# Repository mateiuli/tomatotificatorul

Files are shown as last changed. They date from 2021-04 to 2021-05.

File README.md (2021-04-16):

# tomatotificatorul
A simple automatic balcony plants (tomatos) watering system powered by sun.

# Parts List
## The battery
The battery I chose was a 12V, 1.4Ah, Sealed, Lead Acid Battery. I bought it from [here](https://www.caranda.ro/product/acumulator-12v-1-4ah-fp1214-stationar-agm-vrla/) for ~7$.
The box is designed for this very battery. Its dimensions are the following: 97 x 43 x 52 x 58mm

## The pump
I bought a brand new washer pump compatible with BMW/Mercedes Benz and others. You can easily find it from any car parts vendor. The part code is: FEBI BILSTEIN 23113.

## The solar panel
I found a 5W solar panel with a solid construction and sturdy frame. 

## Electronics

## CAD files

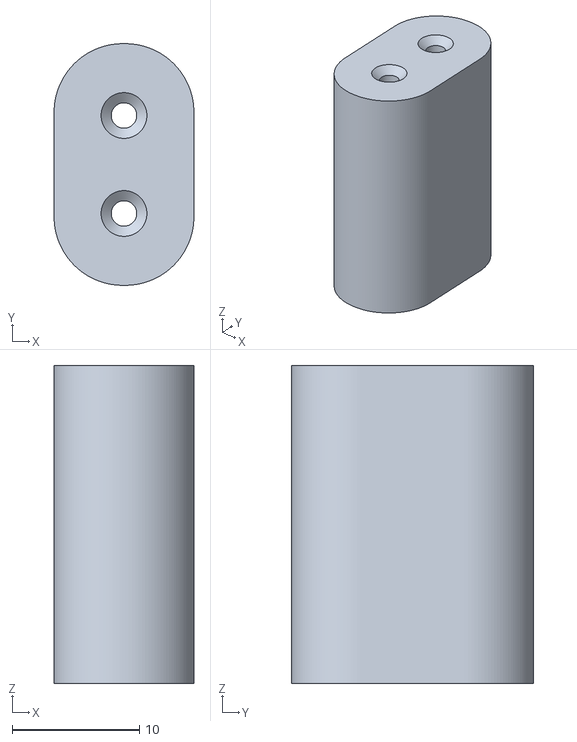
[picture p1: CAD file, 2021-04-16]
3d_objects/12v_pump_plug.stl
11.0 x 19.0 x 25.0

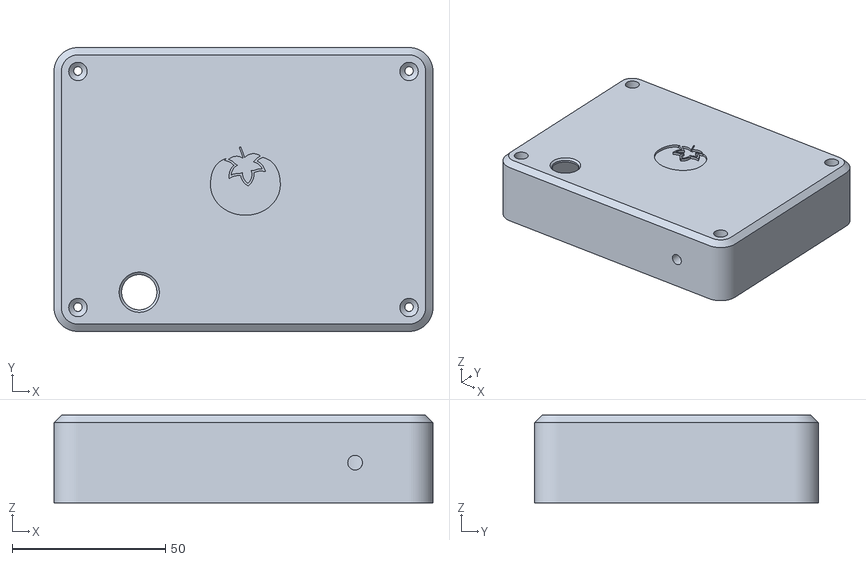
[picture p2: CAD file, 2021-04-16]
3d_objects/box_lid.stl
123.6 x 92.6 x 28.6

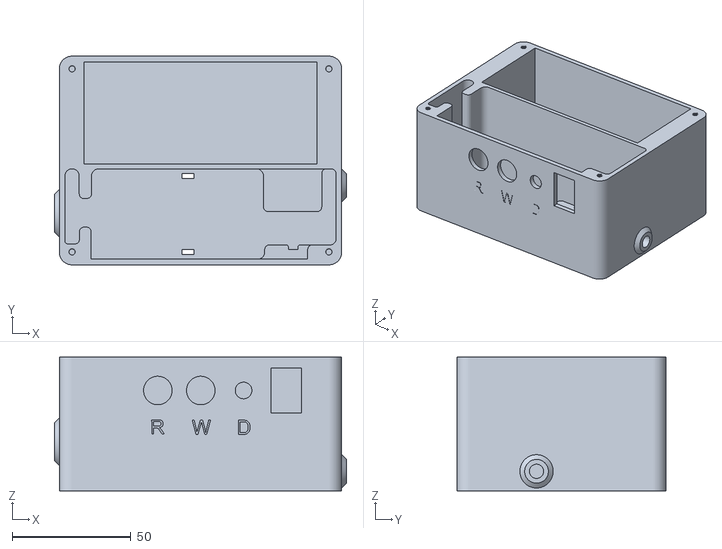
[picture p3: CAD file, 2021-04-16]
3d_objects/box.stl
122.8 x 87.8 x 56.2

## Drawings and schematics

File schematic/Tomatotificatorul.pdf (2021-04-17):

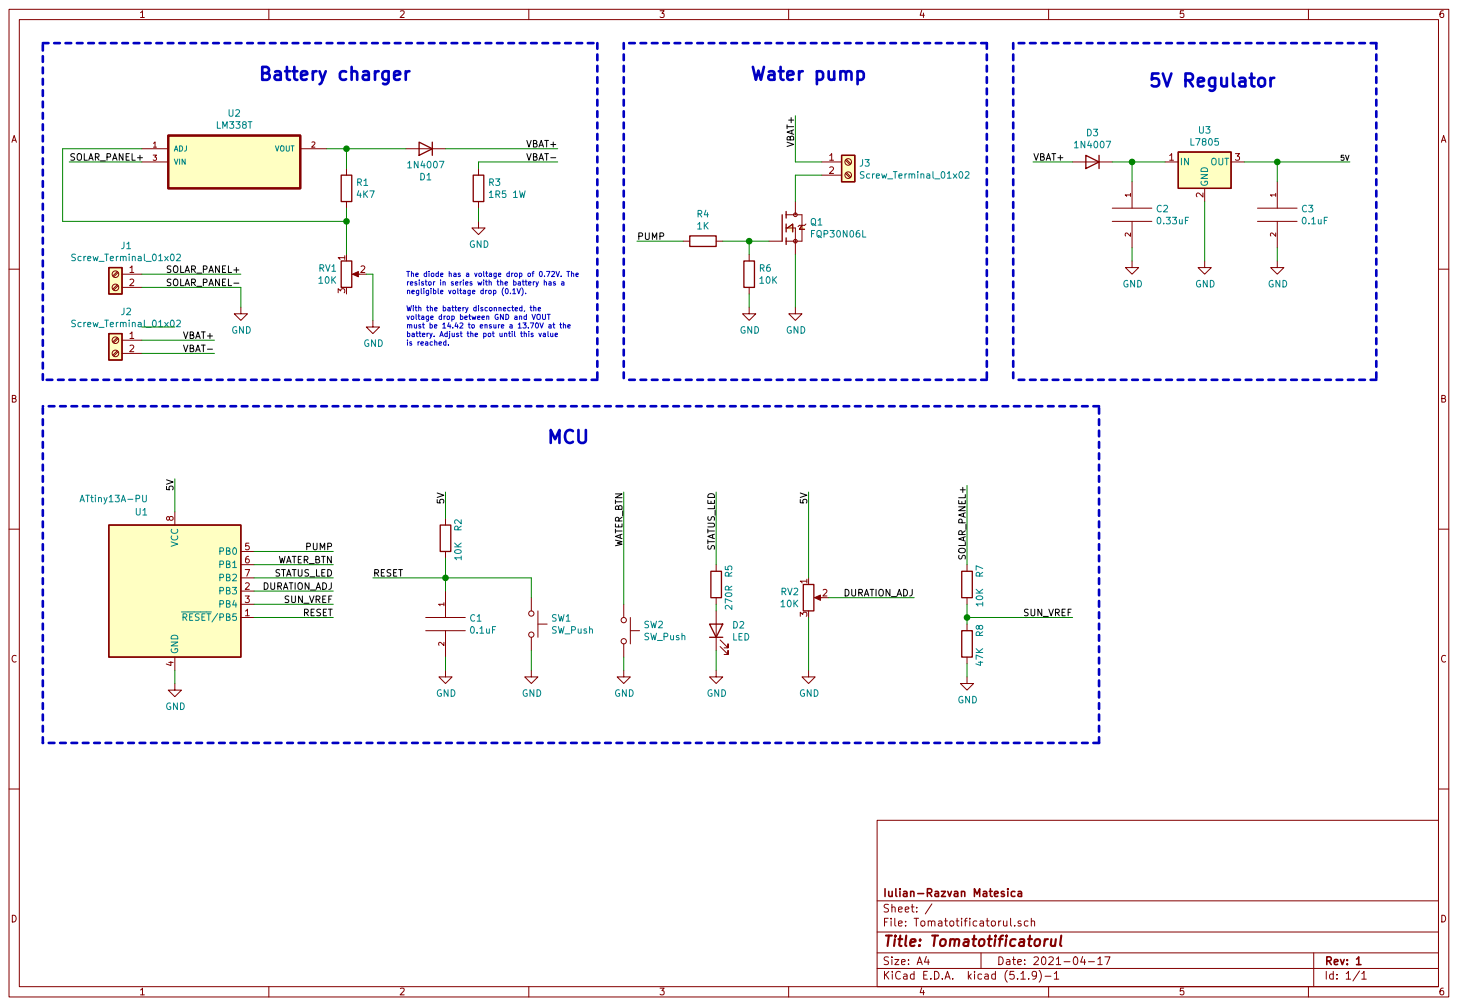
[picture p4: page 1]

1K GND
Iulian-Razvan Matesica SW1 SW_Push GND

The diode has a voltage drop of 0.72V. The resistor in series with the battery has a negligible voltage drop (0.1V). With the battery disconnected, the voltage drop between GND and VOUT must be 14.42 to ensure a 13.70V at the

battery. Adjust the pot until this value

Id: 1/1 Title: Tomatotificatorul File: Tomatotificatorul.sch Sheet: /

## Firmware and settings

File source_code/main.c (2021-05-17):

/****************************************************************************
 * main.c>
 * Tomatotificatorul
 *
 * Copyright 2021 Iulian-Razvan Matesica <iulian.matesica@gmail.com>
 *
 * Licensed under the Apache License, Version 2.0 (the "License");
 * you may not use this file except in compliance with the License.
 * You may obtain a copy of the License at
 * 
 *   http://www.apache.org/licenses/LICENSE-2.0
 * 
 * Unless required by applicable law or agreed to in writing, software
 * distributed under the License is distributed on an "AS IS" BASIS,
 * WITHOUT WARRANTIES OR CONDITIONS OF ANY KIND, either express or implied.
 * See the License for the specific language governing permissions and
 * limitations under the License.
 ****************************************************************************/

/****************************************************************************
 * Included Files
 ****************************************************************************/

#include <avr/io.h>
#include <avr/interrupt.h>
#include <avr/sleep.h>
#include <util/delay.h>

#include <inttypes.h>
#include <stdbool.h>

/****************************************************************************
 * Pre-processor Definitions
 ****************************************************************************/

/* ((64/1200000 * 256 * 73) + (64/1200000 * 135))) = 1s
 * 
 * This is close enough to 1s. The error for 24h is only 2.82s.
 * I can live with that.
 */

// /8
//#define TIMER_OVERFLOW_TICK  587
//#define TIMER_REMAINDER_TICK 255
// o ia inainte cu ~1s / ora 

#define PUMP_ON()  (PORTB |= (1 << PB0))
#define PUMP_OFF() (PORTB &= ~(1 << PB0))

#define STATUS_LED_ON()     (PORTB |= (1 << PB2))
#define STATUS_LED_OFF()    (PORTB &= ~(1 << PB2))
#define STATUS_LED_TOGGLE() (PORTB ^= (1 << PB2))

#define STATUS_LED_LOCK()   (g_led_lock = true)
#define STATUS_LED_UNLOCK() (g_led_lock = false)
#define STATUS_LED_LOCKED() (g_led_lock)

/* If above this threshold, the battery is charging. */

#define SOLAR_PANEL_THRESHOLD 553

// /1 works really well after 1h
// 1s in urma la 1h
//#define TIMER_OVERFLOW_TICK  4709
//#define TIMER_REMAINDER_TICK 196

// -335 ticks == 277us/s = 1s la ora
// 1205700Hz 

#define TIMER_OVERFLOW_TICK  4708
#define TIMER_REMAINDER_TICK 116

//#define TIMER_OVERFLOW_TICK  588
//#define TIMER_REMAINDER_TICK 184


#define HOURLY_ERROR_SEC     1
#define FULL_DAY_TICKS       (((uint32_t)3600 + HOURLY_ERROR_SEC) * 24)

/* This not not precise, it's just an estimation. 
 * Don't use it for precise scheduling. 
 */

#define WATER_EVENT(hour, min, sec) \
    ((uint32_t)3600 * (hour) + \
     (uint32_t)60 * (min) + \
     (sec))

#define MAX(a, b)     ((a) > (b) ? (a) : (b))
#define ARRAY_LEN(a) (sizeof(a) / sizeof(a[0]))

/* Pin mapping::
 *   - PB0 - Pump
 *   - PB1 - Water button
 *   - PB2 - Status LED
 *   - PB3 (ADC3) - Duration adjustment
 *   - PB4 (ADC2) - Solar panel voltage
 */

/****************************************************************************
 * Private Function Prototypes
 ****************************************************************************/

static inline void pump_init(void);
static inline void water_button_init(void);
static inline void status_led_init(void);
static inline void timer_init(void);
static inline void adc_init(void);
static uint16_t adc_read(uint8_t channel);

/****************************************************************************
 * Private Data
 ****************************************************************************/

/* Counts TIMER0 overflows. */

static volatile uint16_t g_overflows;

/* Multiples of 16s since boot-up. */

static volatile uint32_t g_ticks;

/* Set to true from ISR when it's time 
 * to pump some water.
 */

static volatile bool g_water_plant;
static volatile bool g_water_button;
static volatile bool g_led_lock;

static volatile uint8_t g_duration = 5;

/* Add as many "water plant" events as you wish. 
 * Note that the timing is not perfect, it's an estimation, since 
 * the "systick" has a period of 16s.
 */

static const uint32_t g_daily_events[] =
{
    /* WATER_EVENT(hour, minute, second).
     * Important limitation:
     *   If 24h wrap around happens when the pump is on, the pump
     *   will not be stopped. To avoid this, do not add an event 
     *   near the end of the day. 
     */

    WATER_EVENT(0, 0, 5),  /* First event: 5s */
    WATER_EVENT(7, 0, 0),  /* Second event: 7h */
};

/****************************************************************************
 * Private Functions
 ****************************************************************************/

/****************************************************************************
 * Name: pump_init
 *
 * Description:
 *   Initializes the pump. 
 *
 * Input Parameters:
 *   None. 
 *
 * Returned Value:
 *   None.
 *
 ****************************************************************************/

static inline void pump_init(void)
{
    /* Output pin:
     *   0: pump off
     *   1: pump on
     */

    DDRB |= (1 << PB0);
    PORTB &= ~(1 << PB0);
}

/****************************************************************************
 * Name: water_button_init
 *
 * Description:
 *   Configures the water button: interrupt on falling edge, internal 
 *   pull-up resistor enabled.
 *
 * Input Parameters:
 *   None. 
 *
 * Returned Value:
 *   None.
 *
 ****************************************************************************/

static inline void water_button_init(void)
{
    /* Configure INT0 for this button. 
     *   - input pin
     *   - internal pull-up resistor
     */

    DDRB &= ~(1 << PB1);
    PORTB |= (1 << PB1);

    /* Falling edge interrupt. */

    MCUCR |= (2 << ISC00);
    GIMSK |= (1 << INT0);
}

/****************************************************************************
 * Name: INT0_vect
 *
 * Description:
 *   ISR for INT0 - Water button. It is configured to trigger on the 
 *   falling edge. It sets the 'g_water_button' flag to schedule an 
 *   immediate event.
 *
 * Input Parameters:
 *   None. 
 *
 * Returned Value:
 *   None.
 *
 ****************************************************************************/

ISR(INT0_vect)
{
    g_water_button = true;
}

/****************************************************************************
 * Name: status_led_init
 *
 * Description:
 *   Initializes the status LED. 
 *
 * Input Parameters:
 *   None. 
 *
 * Returned Value:
 *   None.
 *
 ****************************************************************************/

static inline void status_led_init(void)
{
    /* Output pin; default off.
     * 
     * Configure and light the status LED 
     * for few seconds.
     */

    DDRB |= (1 << PB2);
}

/****************************************************************************
 * Name: timer_init
 *
 * Description:
 *   Initializes Timer0 to generate both overflow and match interrupts 
 *   which are used to schedule the water events, 2 per day.
 *
 * Input Parameters:
 *   None. 
 *
 * Returned Value:
 *   None.
 *
 ****************************************************************************/

static inline void timer_init(void)
{
    /* 16s period:
     *   - 61 overflows
     *   - 9 remainder ticks
     *   - prescaler 1024
     *   - F_CPU 1MHz
     */

    TCNT0 = 0;
    OCR0A = TIMER_REMAINDER_TICK;
    TIMSK0 |= (1 << TOIE0); 
    TCCR0B |= (1 << CS00);
}

/****************************************************************************
 * Name: TIM0_OVF_vect
 *
 * Description:
 *   Timer0 is free running and this is the ISR for overflow (when it 
 *   reaches 0xFF).
 *
 * Input Parameters:
 *   None. 
 *
 * Returned Value:
 *   None.
 *
 ****************************************************************************/

ISR(TIM0_OVF_vect)
{
    g_overflows++;

    if (g_overflows == TIMER_OVERFLOW_TICK)
    {
        TIMSK0 |= (1 << OCIE0A);
        g_overflows = 0;
    }
}

/****************************************************************************
 * Name: TIM0_COMPA_vect
 *
 * Description:
 *   ISR for Timer0 Output Compare A match interrupt. 
 *   It is used to count the time since boot-up. 
 *
 * Input Parameters:
 *   None. 
 *
 * Returned Value:
 *   None.
 *
 ****************************************************************************/


ISR(TIM0_COMPA_vect)
{
    static volatile uint32_t pump_start_ticks = 0;
   
    /* This interrupt will be enabled again by the 
     * overflow ISR, at the proper time. This way we 
     * don't waste CPU cycles (and power).
     *
     * This function is called every second.
     */

    TIMSK0 &= ~(1 << OCIE0A);
    g_ticks++;

    /* Make sure there is no pumping in progress.
     * We wouldn't want to flood the plants.
     */
    
    if (pump_start_ticks == 0)
    {
        if (g_water_plant)
        {
            /* Water was manually requested. */

            g_water_plant = false;

            /* Start pumping now. */

            pump_start_ticks = g_ticks;
        }
        else 
        {
            /* Was water scheduled at this time? */

            for (int i = 0; i < ARRAY_LEN(g_daily_events); i++)
            {
                if (g_ticks == g_daily_events[i])
                {
                    /* Start pumping now. */

                    pump_start_ticks = g_ticks;
                    break;
                }
            }
        }
    }

    if (pump_start_ticks == g_ticks)
    {
        /* Start the pump. */
        
        PUMP_ON();
        STATUS_LED_LOCK();
        STATUS_LED_ON();
    }

    if (pump_start_ticks != 0)
    {
        /* Pumping in progress. */

        if (g_ticks >= pump_start_ticks + g_duration)
        {
            /* Stop the pump. */

            PUMP_OFF();
            STATUS_LED_OFF();
            STATUS_LED_UNLOCK();

            /* Pumping no longer in progress. */

            pump_start_ticks = 0;
        }
    }

    /* 1 day wrap around to avoid overflows. */

    g_ticks = g_ticks % FULL_DAY_TICKS;
}

/****************************************************************************
 * Name: adc_init
 *
 * Description:
 *   Initializes the ADC and disables the digital block for the 
 *   analog pins. 
 *
 * Input Parameters:
 *   None. 
 *
 * Returned Value:
 *   None.
 *
 ****************************************************************************/

static inline void adc_init(void)
{
    DDRB &= ~((1 << PB3) | (1 << PB4));
    
    /* ADC prescaler 128. */

    ADCSRA |= (7 << ADPS0);

    /* Disable digital block for pins PB3 (ADC3) and PB4 (ADC2). */

    DIDR0 |= (1 << ADC2D) | (1 << ADC3D);
}

/****************************************************************************
 * Name: adc_read
 *
 * Description:
 *   Sample the request ADC channel. 
 *
 * Input Parameters:
 *   channel - The ADC channel to read.
 *
 * Returned Value:
 *   The ADC value in range [0, 1023].
 *
 ****************************************************************************/

static uint16_t adc_read(uint8_t channel)
{
    const uint8_t channel_mask = (1 << MUX1) | (1 << MUX0);
    uint16_t val = 0;

    /* Clear the MUX0 and MUX 1 bits. */
    
    ADMUX &= ~channel_mask;
    ADMUX |= channel & channel_mask;

    /* Turn on the ADC. */

    ADCSRA |= (1 << ADEN);

    /* Start the conversion. */

    ADCSRA |= (1 << ADSC);

    /* Wait for the conversion to end. */
    
    while ((ADCSRA & (1 << ADSC)));
    val = ADC; 

    /* Turn off the ADC. */
    
    ADCSRA &= ~(1 << ADEN);

    return val;
}

/****************************************************************************
 * Public Functions
 ****************************************************************************/

int main(void)
{
    uint32_t prev_tick = 0;

    /* Initialize all subsystems. */

    pump_init();
    
    water_button_init();
    
    adc_init();
    
    timer_init();

    status_led_init();
        
    /* Enable MCU sleep (idle). */

    sleep_enable();

    /* Enable global interrupts. */

    sei();

    while (true)
    {
        if (g_ticks != prev_tick)
        {
            prev_tick = g_ticks;

            /* Debounce water button. */

            if (g_water_button && 
                (PINB & (1 << PB1)) == 0)
            {
                g_water_plant = true;
                g_water_button = false;
            }

            /* Read the duration adjustment potentiometer. */

            uint32_t duration = adc_read(3);

            /* y = ax + b
             *   x = 0 (0V)    => y = 5 sec  => b = 5
             *   x = 1023 (5V) => y = 60 sec
             *
             *  => a = 55 / 1023
             *  => y = 55 / 1023 * x + 5;
             */

            duration = 55 * duration / 1023 + 5;
            
            cli();
            g_duration = duration;
            sei();

            /* Read the solar panel voltage. */

            uint32_t solar_panel = adc_read(2);

            /* R1 = 47K, R2 = 10K.
             *
             * Vref = R2 / (R1 + R2) * Vin
             *
             * Example:
             *   a) Vin = 23V   => Vref = 4.03V (charging)
             *   b) Vin = 15.4V => Vref = 2.70V (charging) 
             *   c) Vin = 15V   => Vref = 2.63V (battery not charging)
             *   d) Vin = 14V   => Vref = 2.45V (battery not charging)
             *
             * ADC has a resolution of 10 bits:
             *  2.70V ... X
             *  5V    ... 1023
             *  => X = 2.70V * 1023 / 5 = 553
             *
             */
            
            if (!STATUS_LED_LOCKED())
            {
                /* The status LED is used for two purposes:
                 *  a) 1s ON, 1s OFF, 1s ON... - during battery charging
                 *  b) 'duration' seconds ON   - when pump is on
                 *  
                 * Duration adjustment has priority.
                 */

                if (solar_panel >= SOLAR_PANEL_THRESHOLD)
                {
                    /* Toggle the status LED while charging. */
                    
                    STATUS_LED_TOGGLE();
                }
                else 
                {
                    STATUS_LED_OFF();
                }
            }
        }

        /* Save some power. */

        sleep_cpu();
    }

    return 0;
}

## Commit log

2021-04-16 Add STLs for Box, Lid and Water Pump Plug
    [12v_pump_plug.stl, box.stl, box_lid.stl]
2021-04-17 Added PDF schematic
2021-05-15 Added status LED management
2021-05-15 Fixed water button debounce
    [main.c]
2021-05-17 Fix a bug - turn off status led when not charging
    [main.c]
